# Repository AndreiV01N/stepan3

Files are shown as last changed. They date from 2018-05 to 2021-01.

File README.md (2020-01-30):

## Hardware ##

- Arduino MEGA 2560 r3
- IMU/AHRS: any of GY-85, GY-521, GY-87
- ESP-01 (ESP8266)
- HC-SR04
- CNC Shield
- 2x A4988 drivers
- 2x NEMA 17HS4401
- 2x 96-mm aluminium wheels w/ 6-mm D-shaft holes
- 6x AA alkaline batteries in a flat battery case

## Software ##

The main program code runs on robot's arduino board. It is placed in arduino/ directory.
The robot can also be controlled and tuned remotely through wi-fi using a simple android app.

**Changes since initial commit:**

- In addition to MPU6050's DMP engine it's been implemented open source AHRS filters (Madgwick/Mahony)
- Added support for some other IMU breakout boards (GY-85, GY-87)
- Onboarded Ultrasonic HC-SR04
- AA's charge control has also been added
- Added useful calibrating and debugging tools (see HOWTOs)
- Optimized DC stepper motors' timers settings as well as speed scaling, improved jumping up mechanics

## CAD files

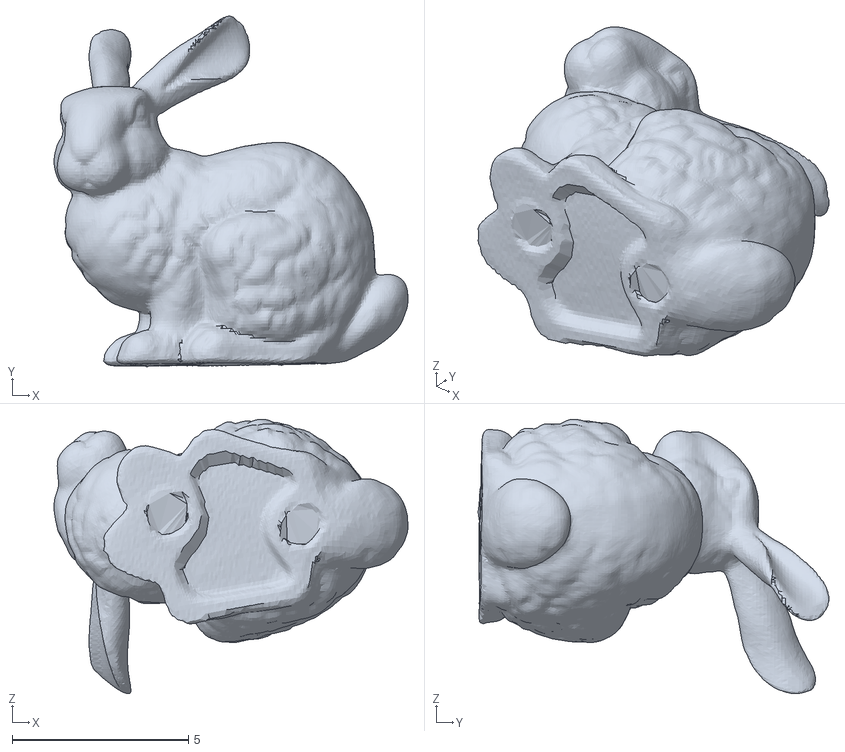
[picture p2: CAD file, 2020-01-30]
arduino/Processing/bunnyrotate/data/bunny.obj
10.0 x 9.94 x 7.77

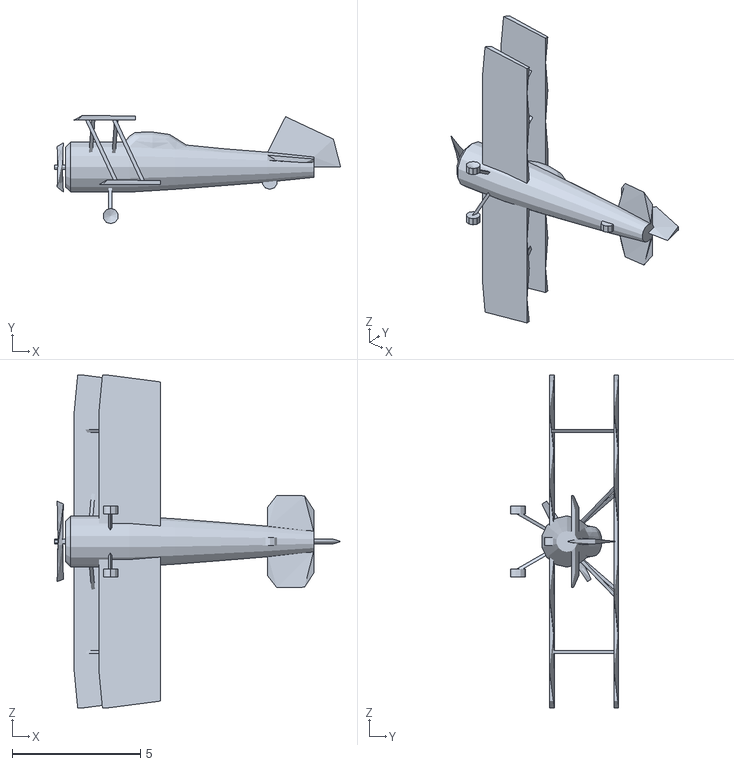
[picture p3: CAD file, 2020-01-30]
arduino/Processing/bunnyrotate/data/biplane.obj
11.2 x 4.23 x 13.0

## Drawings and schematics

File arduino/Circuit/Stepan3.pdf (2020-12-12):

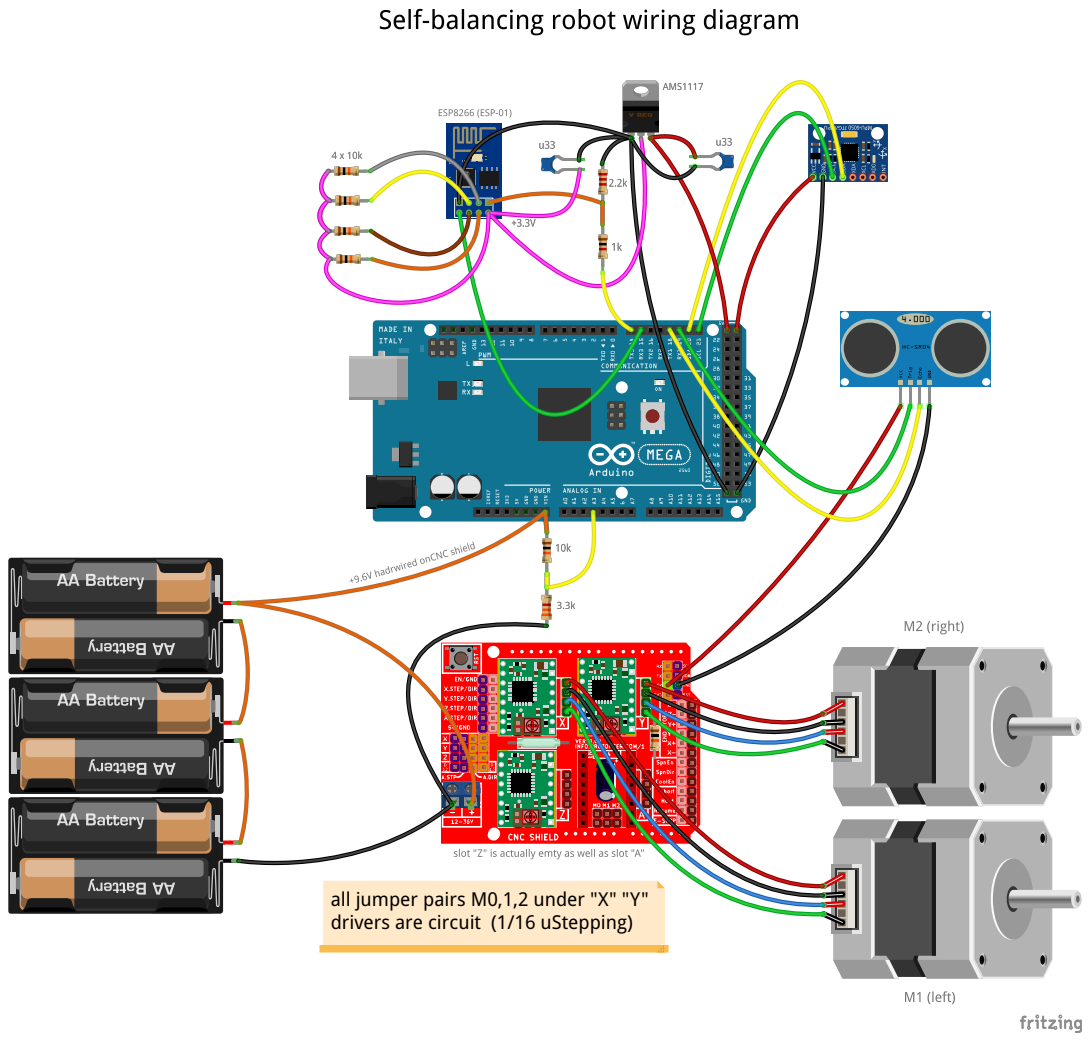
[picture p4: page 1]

all jumper pairs M0,1,2 under "X" "Y"
drivers are circuit (1/16 uStepping)

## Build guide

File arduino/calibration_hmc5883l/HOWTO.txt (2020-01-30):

1. Select needed IMU board, set DEBUG_IMU and DEBUG_IMU_RAW_DATA to 1, recompile and upload the FW.

2. Open "Serial Monitor" in Arduino IDE

3. Rotate the device manually in various directions to accumulate all IMU spatial positions as many as possible.
   The more random data you'll get the better.

4. Copy all the Serial Monitor output into serial_out.log file.

5. Extract raw magnetometer data (X, Y, Z) from serial_out.log to .csv file:
cat ./serial_out.log | grep -E "^Raw" | awk '{print $8","$9","$10}' >./mag_raw.csv

6. Plot the data and check out how it looks
./plot_raw.m

7. Find and remove all odd "dots" dropped out of the "sphere" surface if any:
cat ./mag_raw.csv | sort -t "," -k 1 -g | less
cat ./mag_raw.csv | sort -t "," -k 2 -g | less
cat ./mag_raw.csv | sort -t "," -k 3 -g | less

8. Copy hard iron offsets into code (an appropriate 'imu_*.ino' file):
cat ./mag_raw.cvs | ./cal_hard_iron.py >./mag_hard.csv

9. Copy soft iron offsets into code (same 'imu_*.ino' file):
cat ./mag_hard.csv | ./cal_soft_iron.py >./mag_soft.csv

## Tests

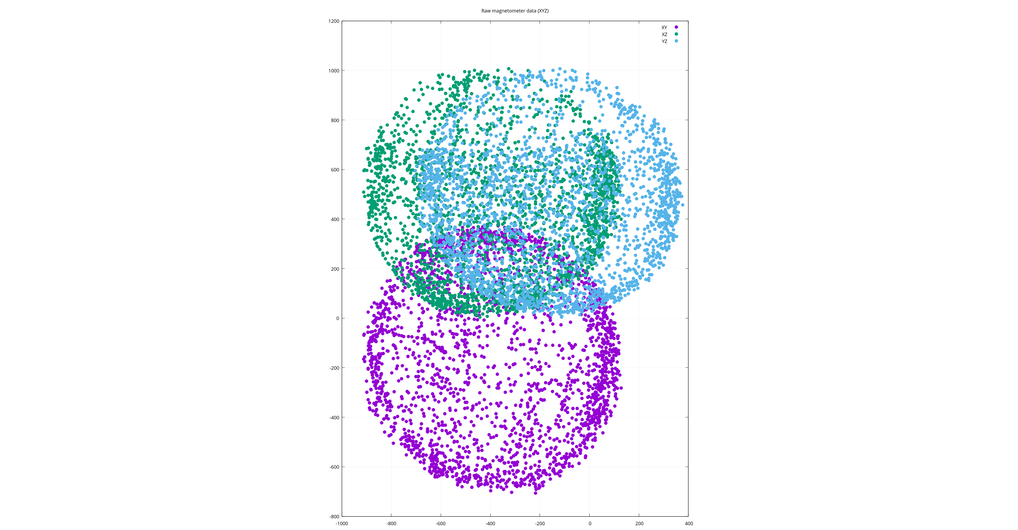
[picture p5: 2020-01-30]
arduino/calibration_hmc5883l/GY_87/mag_raw.png

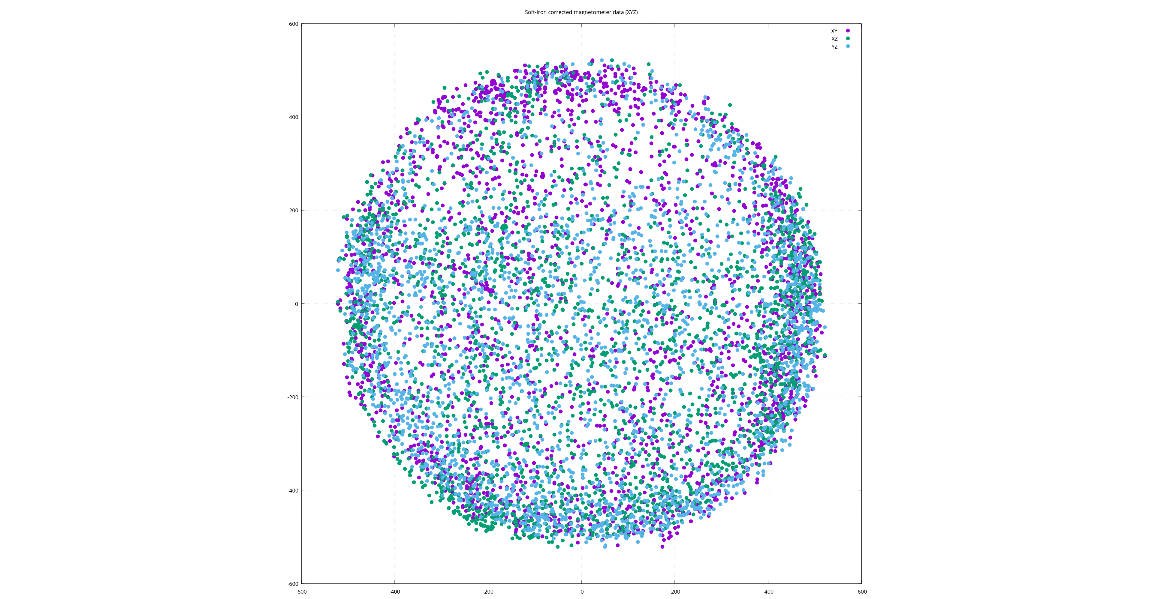
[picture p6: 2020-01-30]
arduino/calibration_hmc5883l/GY_87/mag_soft.png

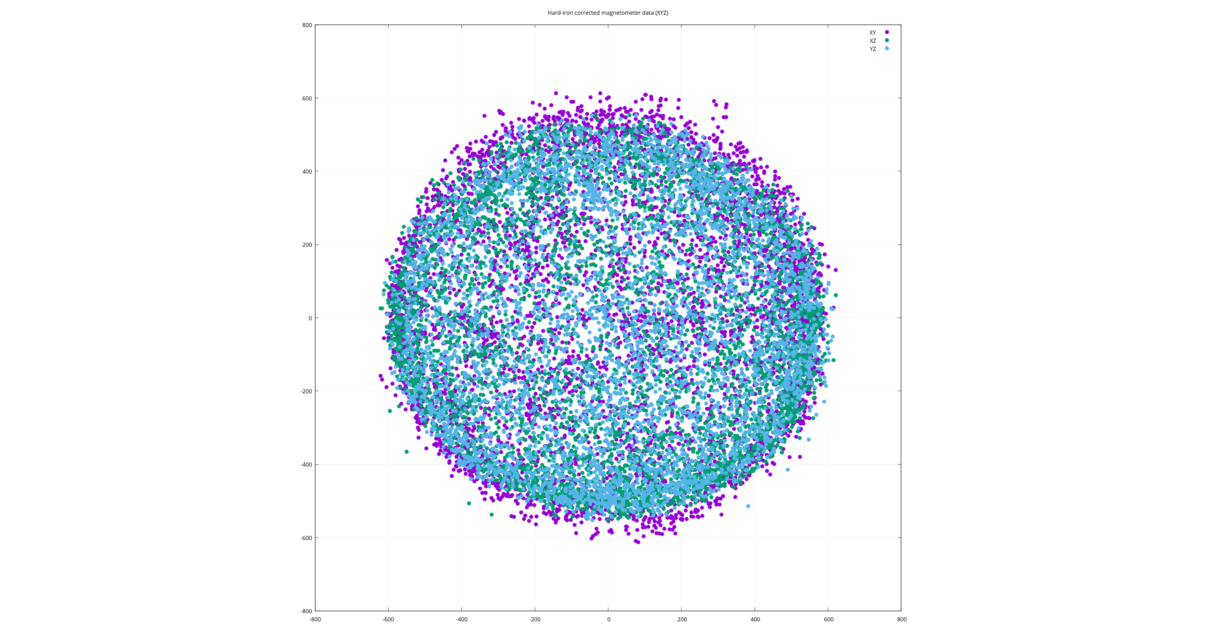
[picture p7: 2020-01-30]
arduino/calibration_hmc5883l/GY_85/mag_hard.png

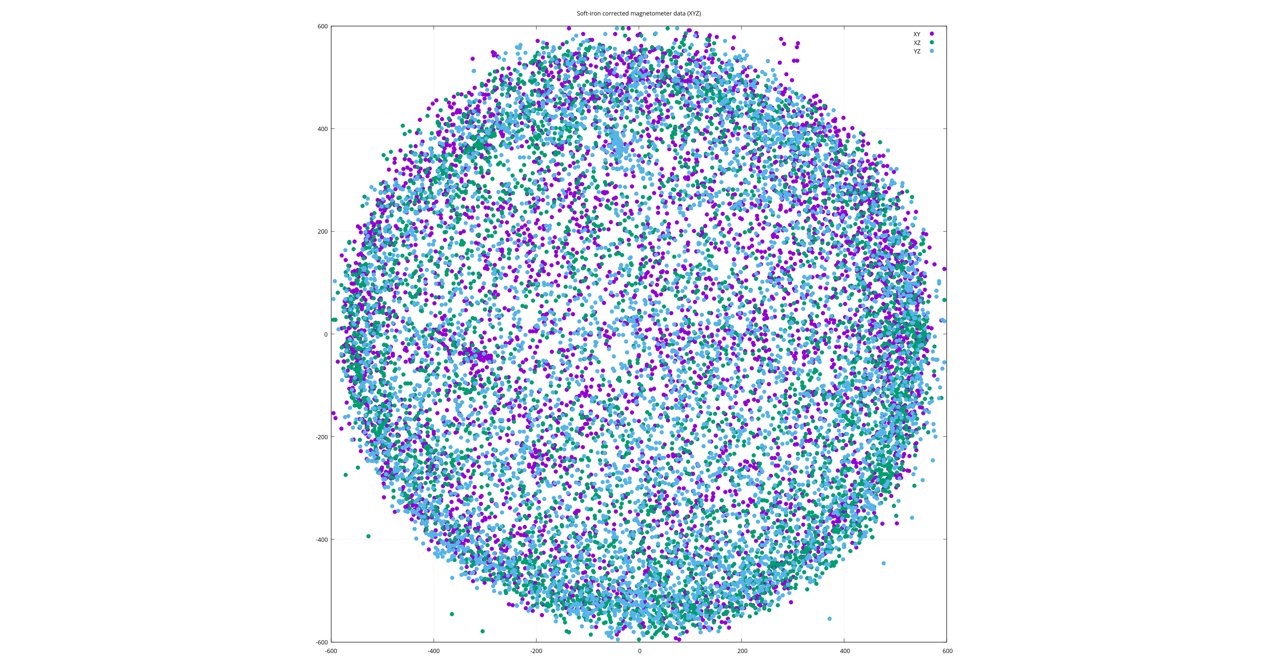
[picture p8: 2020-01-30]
arduino/calibration_hmc5883l/GY_85/mag_soft.png

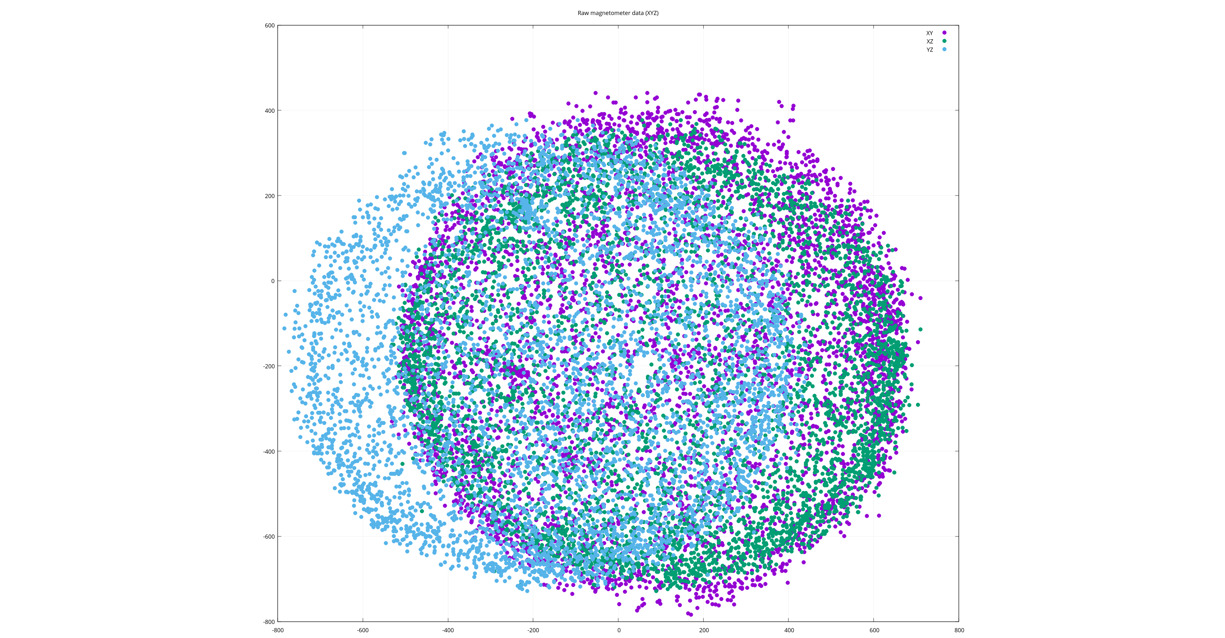
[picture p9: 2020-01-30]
arduino/calibration_hmc5883l/GY_85/mag_raw.png

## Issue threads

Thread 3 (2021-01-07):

imu/ahrs stab-procedure has to be improved

AndreiV01N, 2021-01-07:
__imu_stab() procedure stops on wrong tilt value time to time.

AndreiV01N, 2021-01-11:
Sometimes ```x_delta_sign_now``` (tilt axis delta sign) can change while other axes are still unstable. Thus ```__imu_stab()``` procedure stops on wrong tilt value.
Fix: ```x_delta_sign_ref``` needs to be updated at every comparison with ```x_delta_sign_now``` value.

Closed 2021-01-11.

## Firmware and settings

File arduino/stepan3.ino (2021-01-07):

#define GY_521				0	// available IMU/AHRS boards: GY_521, GY_85, GY_87
#define GY_85				1
#define GY_87				0

#define TILT_AXIS_X			1	// depends on how the IMU/AHRS board is positioned inside
#define TILT_AXIS_Y			0

#define DEBUG_IMU			0	// if this is set to 1, one of 4 below should be set to 1 as well
#define DEBUG_IMU_RAW_DATA		0
#define DEBUG_IMU_PROCESSING_CUBE	0
#define DEBUG_IMU_PROCESSING_BUNNY	0
#define DEBUG_IMU_CALIBRATION		0	// if set to 1 - lock the robot vertically (approx.) and keep it motionless

#define KP_POSITION			0.08f
#define KD_POSITION			0.20f

#define KP_SPEED			0.06f
#define KI_SPEED			0.08f

#if GY_85
#define KP_STAB				0.50f
#define KD_STAB				0.20f
#else
#define KP_STAB				0.30f
#define KD_STAB				0.10f
#endif

#define LOOP_NUM_K_SOFT_START		50	// K*_stab are tuned on first N loops to start smoothly when abs(tilt) < TILT_COMFORT

#define MAX_SPEED_TARGET		140
#define MAX_TILT_TARGET			35
#define MAX_CONTROL_OUTPUT		700

#define MAX_ACCEL_NORMAL		50
#define MAX_DECCEL_NORMAL		200
#define MAX_ACCEL_RISEUP		10
#define MAX_DECCEL_RISEUP		50	// acts the same way as "ABS" in real vehecles

#define MAX_LEN_REMOTE_CMD		6
#define MAX_LEN_REMOTE_CMD_VAL		9

#define TILT_BIAS			-0.0f	// doesn't really matter (helps to prevent onetime short moving drift on start)
#define TILT_READY			60.0f	// robot's tilt is supposed as VERTICAL (within working sector)
#define TILT_COMFORT			15.0f	// relates to LOOP_NUM_K_SOFT_START
#define ROUTE_PAUSE			10000	// time between routes in ms (if standalone)
#define SLEEP_TIMEOUT			2000	// in ms
#define RISEUP_TIMEOUT			1000	// in ms

#define BATTERY_PIN			A3	// 10-bit voltage of 6xAA on BATTERY_PIN (Vbatt -> 10kOhm -> BATTERY_PIN -> 3.3kOhm -> GND)
						// 300 (totally exhausted AAs) ... 450 (new and fresh AAs)

#define ECHO				true
#define NO_ECHO				false

#define RET_ON_EMPTY_BUFF		true
#define NO_RET_ON_EMPTY_BUFF		false

#define MODE				6	// 0 - networkless, standalone
						// 1 - AP, syslog only
						// 2 - AP, remote control only
						// 3 - AP, remote control + syslog
						// 4 - STA, syslog only
						// 5 - STA, remote control only
						// 6 - STA, remote control + syslog

#if MODE == 1
#define WIFI_AP_MODE
#define SYSLOG					// the first connected STA is considered as a syslog-server
#endif

#if MODE == 2
#define WIFI_AP_MODE
#define REMOTE_CTL
#endif

#if MODE == 3
#define WIFI_AP_MODE
#define REMOTE_CTL
#define SYSLOG					// the first connected STA is considered as a syslog-server
#endif

#if MODE == 4
#define WIFI_STA_MODE
#define SYSLOG
#endif

#if MODE == 5
#define WIFI_STA_MODE
#define REMOTE_CTL
#endif

#if MODE == 6
#define WIFI_STA_MODE
#define REMOTE_CTL
#define SYSLOG
#endif

#ifdef SYSLOG
char syslog_msg[255];
#endif

#ifdef REMOTE_CTL
char remote_cmd[MAX_LEN_REMOTE_CMD + 1];		// 6 + 1
char remote_cmd_val[MAX_LEN_REMOTE_CMD_VAL + 1];	// 9 + 1
#endif

float axis_x;				// roll by default (in deg.)
float axis_y;				// pitch by default (in deg.)
float axis_z;				// yaw by default (in deg.)

float tilt_now;				// near zero if vertical, positive if tilt forward (in deg.)
float tilt_target_raw = 0.f;
float tilt_target = 0.f;

float speed_now;			// avg(speed_M1, speed_M2)
float speed_target_raw = 0.f;		// all of speed_* below are in "full steps"/sec (1 wheel rotation eq 200 full steps)
float speed_target = 0.f;		// e.g. speed_target=200 means 1 wheel rotation per second (approx 0.3 m/s)

float dt_f_s;				// loop duty - is used by PID regulators

float Kp_pos = KP_POSITION;
float Kd_pos = KD_POSITION;

float Kp_speed = KP_SPEED;
float Ki_speed = KI_SPEED;

float Kp_stab = KP_STAB;
float Kd_stab = KD_STAB;

float control_output_raw = 0.f;
float control_output = 0.f;		// positive when going forward

float steering_raw;
float steering;

float M1_pos_ctl;
float M2_pos_ctl;

float sonar_dist_cm = 0.f;

int32_t step_M1;			// increases when forward
int32_t step_M2;
int32_t target_step_M1;			// 1 wheel rotation = 300 mm (3200 steps for 1/16 microstepping or 200 steps for "full stepping")
int32_t target_step_M2;
uint32_t dt_ms;	
uint32_t now_us;
uint32_t now_ms;
uint32_t timer_pid_us;
uint32_t timer_loop_ms;
uint32_t timer_riseup_ms;
uint32_t timer_route_ms;
uint32_t timer_sleep_ms;
uint32_t loop_number = 0;

int16_t max_accel = MAX_ACCEL_NORMAL;
int16_t max_deccel = MAX_DECCEL_NORMAL;
int16_t control_M1;
int16_t control_M2;
int16_t speed_M1;			// actual speed of M1 (positive when going forward)
int16_t speed_M2;
uint16_t battery_raw;

int8_t dir_M1;				// actual direction of M1 (positive when rotates forward, zero if stops)
int8_t dir_M2;
uint8_t route_point = 0;		// current route segment (see route.ino)
uint8_t riseup_phase = 0;

bool is_awake = false;			// 'true' means the robot is not asleep and ready to any activities
bool position_up = false;		// 'true' means actual 'tilt_now' value < abs(TILT_READY) - i.e. we are UP
bool on_route = false;			// 'true' means the robot is now following predefined route path
bool on_riseup = false;			// 'true' means the robot is now trying to reach abs(TILT_READY) from laying position
bool on_control = false;		// 'true' means robot's movements are now controlled remotely
bool on_soft_start = false;		// 'true' means Kp_stab and Kd_stab are being corrected
bool is_sta_online = false;
bool is_sonar_ready = true;


int16_t my_round(float x)
{
	return (int)(x + (x < 0 ? -0.5f : 0.5f));
}


void append_float_to_str(char *str, const char *tag, float f, const uint8_t prec)
{
	strcat(str, tag);
	dtostrf(f, prec + 5, prec, str + strlen(str));
}


float get_tilt()
{
#if TILT_AXIS_X
	return (axis_x - TILT_BIAS);
#elif TILT_AXIS_Y
	return (axis_y - TILT_BIAS);
#endif
}


void setup()
{
	Serial.begin(115200);
	Serial3.begin(115200);

#if DEBUG_IMU
	imu_init();						// can take a few seconds
#else

#ifdef WIFI_STA_MODE
	esp8266_connect_to_ap();
	esp8266_ipservices_init();
#endif

#ifdef WIFI_AP_MODE
	esp8266_init_local_ap();

	while (!is_sta_online) {
		is_sta_online = esp8266_is_any_sta_online();
		delay(1000);
	}

	esp8266_ipservices_init();
#endif

	motor_pins_init();
	sonar_pins_init();
	delay(100);
	imu_init();
	imu_read_data();
	tilt_now = get_tilt();

	if (fabs(tilt_now) < TILT_READY) {			// an initial position is UP
		position_up = true;
		is_awake = true;
		timer_route_ms = millis();
		timer_pid_us = micros();
		if (fabs(tilt_now) < TILT_COMFORT)
			on_soft_start = true;
	} else {
		position_up = false;
		stall();
	}

	timer_loop_ms = millis();
#endif		// not DEBUG_IMU
}


void loop()
{
#if DEBUG_IMU

#if !DEBUG_IMU_CALIBRATION					// do nothing in the loop() while calibrating
	imu_read_data();
#endif

#else	// not DEBUG_IMU
	imu_read_data();
	tilt_now = get_tilt();

	if (fabs(tilt_now) < TILT_READY) {			// we are now UP (within tilt working sector)
		if (position_up) {				// last time we were UP as well
			if (is_awake) {
				// this helps a lot to avoid moving twitches on early start being UP
				if (on_soft_start && loop_number <= LOOP_NUM_K_SOFT_START) {
					Kp_stab = KP_STAB * loop_number / LOOP_NUM_K_SOFT_START;
					Kd_stab = KD_STAB * loop_number / LOOP_NUM_K_SOFT_START;
					if (loop_number == LOOP_NUM_K_SOFT_START)
						on_soft_start = false;
				}
#ifndef REMOTE_CTL
				if (!on_route) {
					dt_ms = millis() - timer_route_ms;
					if (dt_ms > ROUTE_PAUSE) {
						on_route = true;
						route_point = 0;
					}
				}
#endif
			} else {				// received 'Sleep' remote command earlier while being UP
				set_speed_M1(0);
				set_speed_M2(0);
				dt_ms = millis() - timer_sleep_ms;
				if (dt_ms > SLEEP_TIMEOUT)
					is_awake = true;
			}
		} else {					// we've just got UP, needs to set normal params
			step_M1 = 0;
			step_M2 = 0;
			position_up = true;
			is_awake = true;
			on_riseup = false;
			riseup_phase = 0;
			max_accel = MAX_ACCEL_NORMAL;
			max_deccel = MAX_DECCEL_NORMAL;
			timer_route_ms = millis();
			timer_pid_us = micros() - 10000;	// set pid timer 10ms behind
			pid_reset_errors();
		}
	} else {						// we are now DOWN (out of tilt working sector)
		if (position_up) {				// just fell over for any reasons (last time we were UP)
			on_route = false;
			on_control = false;
			position_up = false;
			on_riseup = false;
			if (is_awake)				// fell over on its own (it was not a 'Sleep' remote command)
				stall();
			else {					// we're already asleep - just keep falling down after receiving 'Sleep' cmd
				set_speed_M1(0);
				set_speed_M2(0);
				dt_ms = millis() - timer_sleep_ms;
				if (dt_ms > SLEEP_TIMEOUT)
					is_awake = true;
			}
		} else {					// last time we were DOWN too (we're still out of tilt working sector)
			if (is_awake) {
				if (on_riseup) {		// here we're keep trying to get UP
					riseup_control();
					dt_ms = millis() - timer_riseup_ms;
					if (dt_ms > RISEUP_TIMEOUT)		// we've not managed to reach tilt working sector in time..
						stall();
				}
			} else {				// in 'sleep' state due to stall() called or it's robot's initial pos
				set_speed_M1(0);
				set_speed_M2(0);
				dt_ms = millis() - timer_sleep_ms;
				if (dt_ms > SLEEP_TIMEOUT) {
					is_awake = true;
#ifndef REMOTE_CTL
					on_riseup = true;	// auto-riseup if standalone
#endif
				}
			}
		}
	}

	speed_now = float(speed_M1 + speed_M2) / 2.f;

	if (position_up && is_awake) {
		if (on_route) {
			follow_route();				// updates target_step_M*
			M1_pos_ctl = position_PD_control(step_M1, target_step_M1, Kp_pos, Kd_pos, speed_M1);
			M2_pos_ctl = position_PD_control(step_M2, target_step_M2, Kp_pos, Kd_pos, speed_M2);

			speed_target_raw = (M1_pos_ctl + M2_pos_ctl) / 2;
			speed_target     = constrain(speed_target_raw, -MAX_SPEED_TARGET, MAX_SPEED_TARGET);
		} else if (!on_control)
			speed_target = 0;

		now_us = micros();
		dt_f_s = (float)(now_us - timer_pid_us) / 1000000.f;
		timer_pid_us = now_us;

		tilt_target_raw = speed_PI_control(dt_f_s, speed_now, speed_target, Kp_speed, Ki_speed);
		tilt_target     = constrain(tilt_target_raw, -MAX_TILT_TARGET, MAX_TILT_TARGET);		// -35..+35

		control_output_raw += stability_PD_control(dt_f_s, tilt_now, tilt_target, Kp_stab, Kd_stab);
		control_output      = constrain(control_output_raw, -MAX_CONTROL_OUTPUT, MAX_CONTROL_OUTPUT);	// -700..+700

		if (on_route)
			steering = get_steering();
		else if (!on_control)
			steering = 0;

		control_M1 = my_round(control_output + steering);
		control_M2 = my_round(control_output - steering);

		set_speed_M1(control_M1);
		set_speed_M2(control_M2);

		if (is_sonar_ready)
			sonar_send_ping();
	}

	battery_raw = analogRead(BATTERY_PIN);

	loop_number++;
	now_ms = millis();
	dt_ms = now_ms - timer_loop_ms;
	timer_loop_ms = now_ms;

#ifdef SYSLOG
/*
Attention!
Too many params here increases loop duty time a lot.
Ideally dt_ms value should not exceed 16-17 ms.
Otherwise you'll face some tremors and other misbehaves..
*/

	sprintf(syslog_msg + strlen(syslog_msg), " LPN: %lu", loop_number);
	sprintf(syslog_msg + strlen(syslog_msg), " LPT: %lu", dt_ms);
//	sprintf(syslog_msg + strlen(syslog_msg), " BAT: %u", battery_raw);

//	append_float_to_str(syslog_msg, " DST: ", sonar_dist_cm, 2);
	append_float_to_str(syslog_msg, " SPD: ", speed_now, 2);
//	append_float_to_str(syslog_msg, " SPDt: ", speed_target, 2);
	append_float_to_str(syslog_msg, " TLT: ", tilt_now, 2);
	append_float_to_str(syslog_msg, " TLTt: ", tilt_target, 2);
	append_float_to_str(syslog_msg, " COUT: ", control_output, 2);
//	append_float_to_str(syslog_msg, " YAW: ", axis_z, 2);

	logger_telemetry(syslog_msg);
#elif defined REMOTE_CTL
	esp8266_rx_buff_parser_wrapper(8, remote_cmd, __parse_loop_data, RET_ON_EMPTY_BUFF, NO_ECHO);
#endif

#endif	// not DEBUG_IMU
}

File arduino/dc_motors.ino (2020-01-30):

#define M1_STEP_PIN		2			// PE4
#define M2_STEP_PIN		3			// PE5
#define M1_DIR_PIN		5			// PE3
#define M2_DIR_PIN		6			// PH3
#define	CNC_ENABLED_PIN		8			// PH5

#define ZERO_SPEED		65535
#define RISEUP_SPEED		500
#define RISEUP_BRAKE		5
#define MICROSTEPPING		4			// power of 2 for 16, 8, 4, 2, 1 (i.e. 4 means 1/16, 0 means "full stepping")
							// must fit to jumpers' settings on CNC-shield
#define TIMER_CLOCK		250000			// (Hz) configured in TCCR1B, TCCR3B registers

/*
	2 x 17HS4401 - Rated current: 1.7A
	microstepping:		FULL	1/2	1/4	1/8	1/16
	steps/rotation:		200	400	800	1600	3200
	degree/step		1.8	0.9	0.45	0.225	0.1125

	2 x A4988, Rs = 0.1 Ohm, Vref has to be set near 0.95V
*/

#include <avr/io.h>


/* http://www.atmel.com/Images/Atmel-2549-8-bit-AVR-Microcontroller-ATmega640-1280-1281-2560-2561_datasheet.pdf
   STEP_M1: D2 (PE4), DIR_M1: D5 (PE3) as outputs (step controlled by TIMER-1) CNC SHIELD-X
   STEP_M2: D3 (PE5), DIR_M2: D6 (PH3) as outputs (step controlled by TIMER-3) CNC SHIELD-Y
   (both motors are driven by A4988)
*/
void motor_pins_init()
{
	Serial.println("Stepper motors initialization...");

	pinMode(M1_STEP_PIN, OUTPUT);			// PE4
	pinMode(M2_STEP_PIN, OUTPUT);			// PE5
	pinMode(M1_DIR_PIN, OUTPUT);			// PE3
	pinMode(M2_DIR_PIN, OUTPUT);			// PH3
	pinMode(CNC_ENABLED_PIN, OUTPUT);		// PH5

	TCCR1A = 0;					// OC1A, OC1B, OC1C pins are disconnected
	TCCR1B = _BV(WGM12) | _BV(CS11) | _BV(CS10);	// Timer1 mode 4 (CTC), Prescaler=64 (clk_io/64 = 250kHz)
	OCR1A = ZERO_SPEED;				// M1 stopped (16-bit)
	speed_M1 = 0;
	step_M1 = 0;
	dir_M1 = 0;
	TCNT1 = 0;

	TCCR3A = 0;					// OC3A, OC3B, OC3C pins are disconnected
	TCCR3B = _BV(WGM32) | _BV(CS31) | _BV(CS30);	// Timer3 mode 4 (CTC), Prescaler=64 (clk_io/64 = 250kHz)
	OCR3A = ZERO_SPEED;				// M2 stopped (16-bit)
	speed_M2 = 0;
	step_M2 = 0;
	dir_M2 = 0;
	TCNT3 = 0;

	PORTH &= ~_BV(5);				// PH5 is LOW (enable motors)
	TIMSK1 |= _BV(OCIE1A);				// Enable Timer1 interrupt
	TIMSK3 |= _BV(OCIE3A);				// Enable Timer3 interrupt

	return;
}


ISR(TIMER1_COMPA_vect)		// M1
{
	if (dir_M1 == 0)	// zero speed
		return;

	PORTE |= _BV(4);	// HIGH

	if (dir_M1 > 0)
		step_M1++;
	else
		step_M1--;

	PORTE &= ~_BV(4);	// LOW
}


ISR(TIMER3_COMPA_vect)		// M2
{
	if (dir_M2 == 0)	// zero speed
		return;

	PORTE |= _BV(5);	// HIGH

	if (dir_M2 > 0)
		step_M2++;
	else
		step_M2--;

	PORTE &= ~_BV(5);	// LOW
}


void set_speed_M1(int16_t tspeed)
{
	int32_t timer_period;
	int16_t speed;

	if (tspeed == speed_M1)
		return;

	if (speed_M1 >= 0) {							// going fwd or stopped
		if (speed_M1 < tspeed) {					// speedup (accel) to fwd
			if ((tspeed - speed_M1) < max_accel)
				speed_M1 = tspeed;
			else
				speed_M1 += max_accel;
		} else {							// slow down (deccel)
			if ((speed_M1 - tspeed) < max_deccel)
				speed_M1 = tspeed;
			else
				speed_M1 -= max_deccel;
		}
	} else {								// going back
		if (tspeed < speed_M1) {					// speedup (accel) to bck
			if ((speed_M1 - tspeed) < max_accel )
				speed_M1 = tspeed;
			else
				speed_M1 -= max_accel;
		} else {							// slow down (deccel)
			if ((tspeed - speed_M1) < max_deccel)
				speed_M1 = tspeed;
			else
				speed_M1 += max_deccel;
		}
	}

	speed = speed_M1 << MICROSTEPPING;		/* cast to real motor speed in u-steps/sec
							TIMER_CLOCK = 250 kHz:

							uSTEPPING = 16 (*is used)
							min speed = 1 << 4      = 16    steps/sec, OCRnA = 250000/16    = 15625
							max speed = 700 << 4    = 11200 steps/sec, OCRnA = 250000/11200 = 22

							uSTEPPING = 8
							min speed = 1 << 3      = 8     steps/sec, OCRnA = 250000/8     = 31250
							max speed = 700 << 3    = 5600  steps/sec, OCRnA = 250000/5600  = 45

							uSTEPPING = 4
							min speed = 1 << 2      = 4     steps/sec, OCRnA = 250000/4     = 62500
							max speed = 700 << 2    = 2800  steps/sec, OCRnA = 250000/2800  = 89
							*/
	if (speed == 0) {
		timer_period = ZERO_SPEED;
		dir_M1 = 0;
	} else if (speed > 0) {
		timer_period = TIMER_CLOCK / speed;
		dir_M1 = 1;
		PORTE &= ~_BV(3);			// LOW - DIR M1 (Forward)
	} else {
		timer_period = TIMER_CLOCK / -speed;
		dir_M1 = -1;
		PORTE |= _BV(3);			// HIGH - DIR M1 (Reverse)
	}

	if (timer_period > ZERO_SPEED)			// Check for minimun speed (maximum period without overflow)
		timer_period = ZERO_SPEED;

	OCR1A = timer_period;
	if (TCNT1 > OCR1A)				// Check if we need to reset the timer
		TCNT1 = 0;
}


void set_speed_M2(int16_t tspeed)
{
	int32_t timer_period;
	int16_t speed;

	if (tspeed == speed_M2)
		return;

	if (speed_M2 >= 0) {							// going fwd or stopped
		if (speed_M2 < tspeed) {					// speedup (accel) to fwd
			if ((tspeed - speed_M2) < max_accel)
				speed_M2 = tspeed;
			else
				speed_M2 += max_accel;
		} else {							// slow down (deccel)
			if ((speed_M2 - tspeed) < max_deccel)
				speed_M2 = tspeed;
			else
				speed_M2 -= max_deccel;
		}
	} else {								// going back
		if (tspeed < speed_M2) {					// speedup (accel) to bck
			if ((speed_M2 - tspeed) < max_accel )
				speed_M2 = tspeed;
			else
				speed_M2 -= max_accel;
		} else {							// slow down (deccel)
			if ((tspeed - speed_M2) < max_deccel)
				speed_M2 = tspeed;
			else
				speed_M2 += max_deccel;
		}
	}

	speed = speed_M2 << MICROSTEPPING;		// cast to real motor speed in steps/sec

	if (speed == 0) {
		timer_period = ZERO_SPEED;
		dir_M2 = 0;
	} else if (speed > 0) {
		timer_period = TIMER_CLOCK / speed;
		dir_M2 = 1;
		PORTH |= _BV(3);			// HIGH - DIR M2 (Forward)
	} else {
		timer_period = TIMER_CLOCK / -speed;
		dir_M2 = -1;
		PORTH &= ~_BV(3);			// LOW - DIR M2 (Reverse)
	}

	if (timer_period > ZERO_SPEED)			// Check for minimun speed (maximum period without overflow)
		timer_period = ZERO_SPEED;

	OCR3A = timer_period;
	if (TCNT3 > OCR3A)				// Check if we need to reset the timer
		TCNT3 = 0;
}


void stall()
{
	set_speed_M1(0);
	set_speed_M2(0);
	on_riseup = false;
	is_awake = false;
	riseup_phase = 0;
	control_output = 0.f;
	control_output_raw = 0.f;
	timer_sleep_ms = millis();
//	PORTH |= _BV(5);				// PH5 is HIGH (disable motors)
}
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

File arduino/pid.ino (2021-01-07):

#define POSITION_PTERM_MAX	40.0f
#define SPEED_ERROR_MAX		30.0f
#define SPEED_ITERM_MAX		10000.0f
#define STAB_DELTA_ERROR_MAX	8.0f

static float speed_i_error = 0.f;
static float tilt_error_last = 0.f;

/*
 Input: step error
 Output: speed_target
*/
float position_PD_control(int32_t input, int32_t setpoint, float Kp, float Kd, int16_t speedM)
{
	float position_error = setpoint - input;
	float pTerm = constrain(Kp * position_error, -POSITION_PTERM_MAX, POSITION_PTERM_MAX);

	float dTerm = Kd * float(speedM);

	return pTerm + dTerm;
}

/*
 Input: speed error
 Output: tilt_target
*/
float speed_PI_control(float dt_s, float input, float setpoint, float Kp, float Ki)
{
	float speed_error = setpoint - input;
	float pTerm = Kp * speed_error;

	speed_i_error += constrain(speed_error, -SPEED_ERROR_MAX, SPEED_ERROR_MAX);
	speed_i_error  = constrain(speed_i_error, -SPEED_ITERM_MAX, SPEED_ITERM_MAX);
	float iTerm = Ki * speed_i_error * dt_s;
#ifdef SYSLOG
	append_float_to_str(syslog_msg, " spP: ", pTerm, 2);
	append_float_to_str(syslog_msg, " spI: ", iTerm, 2);
#endif
	return pTerm + iTerm;
}

/*
 Input: tilt_error
 Output: delta of control_output
*/
float stability_PD_control(float dt_s, float input, float setpoint, float Kp, float Kd)
{
	float tilt_error = input - setpoint;
	float pTerm = Kp * tilt_error;

	float tilt_error_delta = constrain(tilt_error - tilt_error_last, -STAB_DELTA_ERROR_MAX, STAB_DELTA_ERROR_MAX);
	float dTerm = Kd * tilt_error_delta / dt_s;
	tilt_error_last = tilt_error;
#ifdef SYSLOG
	append_float_to_str(syslog_msg, " coP: ", pTerm, 2);
	append_float_to_str(syslog_msg, " coD: ", dTerm, 2);
#endif
	return pTerm + dTerm;
}


void pid_reset_errors()
{
	speed_i_error = 0.f;
	tilt_error_last = 0.f;
	return;
}

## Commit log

2018-06-08 * Added PID-tuning, toggled control buttons, some minor fixes
2020-01-30 * See README.md
    [biplane.obj, bunny.obj, mag_hard.csv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]
2020-01-31 * Automated PID-bars scaling in android app
2020-03-16 * Fixed RC(Arduino) ActionFilter(Android) bugs, hide/unhide joystic view
    [wifi.ino]
2020-09-17 + Added a wiring diagram
    [Stepan3.fzz]
2020-09-22 * Replaced circuit with .pdf, minor fix in remote_cc.ino
    [Stepan3.fzz]
2020-12-12 * Updated schematics
2021-01-07 _#1: improved networking, syslog'ing; fixed minor UI issues in android app
    [imu_gy521.ino, imu_gy85.ino, imu_gy87.ino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]
2021-01-07 _#3: Amended IMU/AHRS STAB procedure

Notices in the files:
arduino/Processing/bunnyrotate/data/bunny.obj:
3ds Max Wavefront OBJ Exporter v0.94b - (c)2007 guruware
